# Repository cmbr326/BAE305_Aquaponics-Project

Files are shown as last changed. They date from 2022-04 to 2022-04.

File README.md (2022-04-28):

# BAE305_Aquaponics.Project

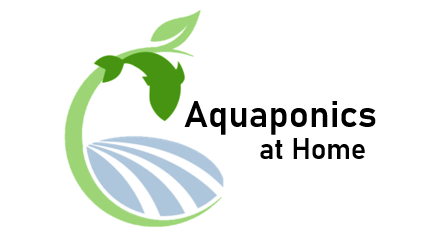
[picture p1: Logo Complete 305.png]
 

## Summary:

   The purpose of this project is to have an autonomous aquaponics system which includes an autonomous fish tank and plant growing environment. The two systems, the fish tank and the garden, work together by providing and filtering water for each other. The water from the fish tank is pumped into the garden when the soil moisture drops below a certain level, and the excess water from the garden precipitates back into the fish tank. Each of these components is vital to keep a livable environment for the fish while also benefiting the plants. The system comes equipped with a grow lamp to give the plants the light that they need on a scheduled basis. Each sensor in the aquaponics system includes displays for the user to properly monitor the vital aspects of the plants and fish's environment.
  
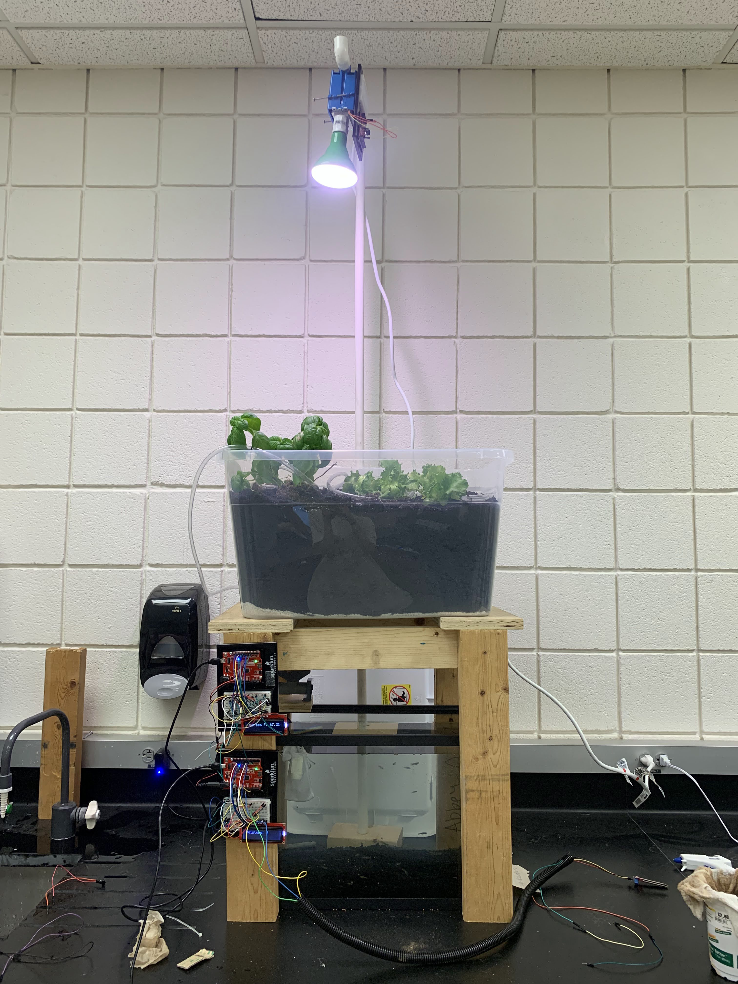
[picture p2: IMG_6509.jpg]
  
 
## Design Description: 

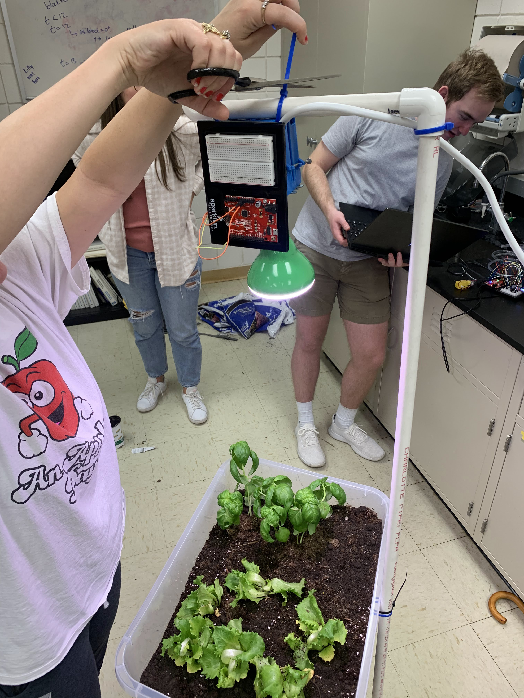
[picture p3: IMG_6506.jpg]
  
  
#### Supplies
- Arduino Uno (3)
- Water Pump (3V-5V Submersible Motor Pump)
- Motor (ElectroPeak DC Gear Motor)
- Temperature sensor (DS18B20 Temperature Sensor) 
- Soil Moisture sensor (SparkFun Soil Moisure Sensor with screw terminals SEN-13637)
- Light bulb
- Mobile outlet
- Fish tank
- Gravel 
- Fish
- Fish food 
- Large tote 
- Mesh screen
- Wood for suspension system
- Tubing 

#### Wiring Diagrams
Fish Tank Circuits


 
Soil Moisture Diagram

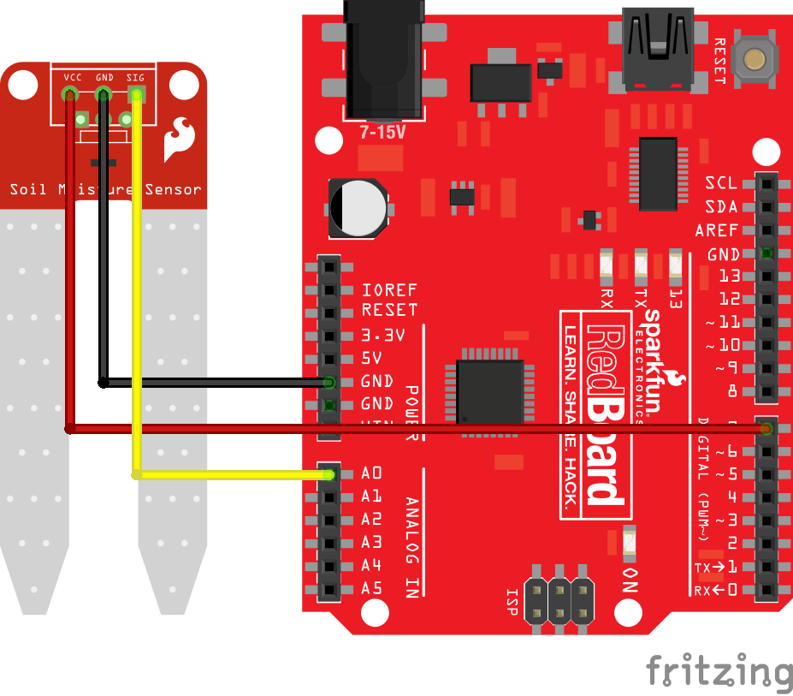
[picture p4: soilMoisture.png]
   
 
Soil Moisture Sensor and Pump 

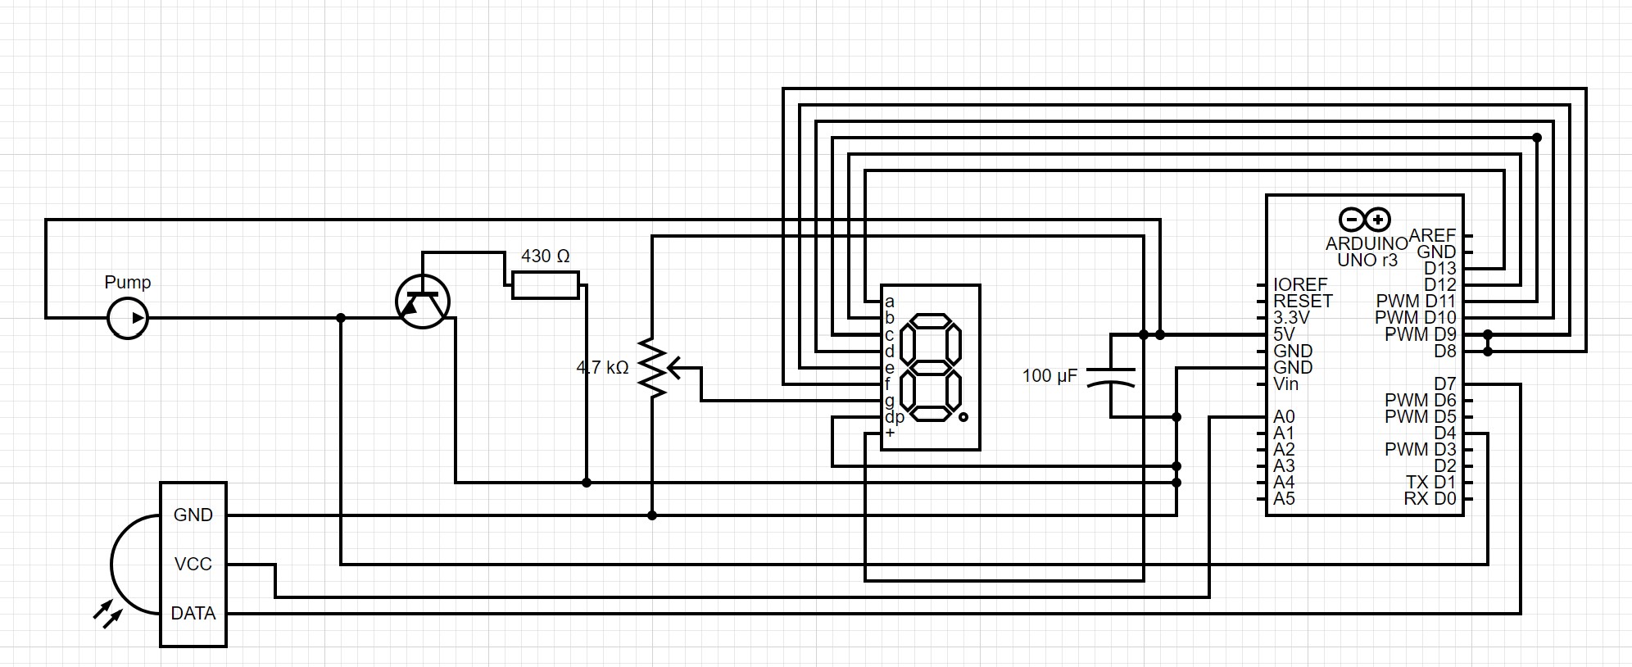
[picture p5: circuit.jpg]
   
 
 Temperature and Humidity Sensor
 
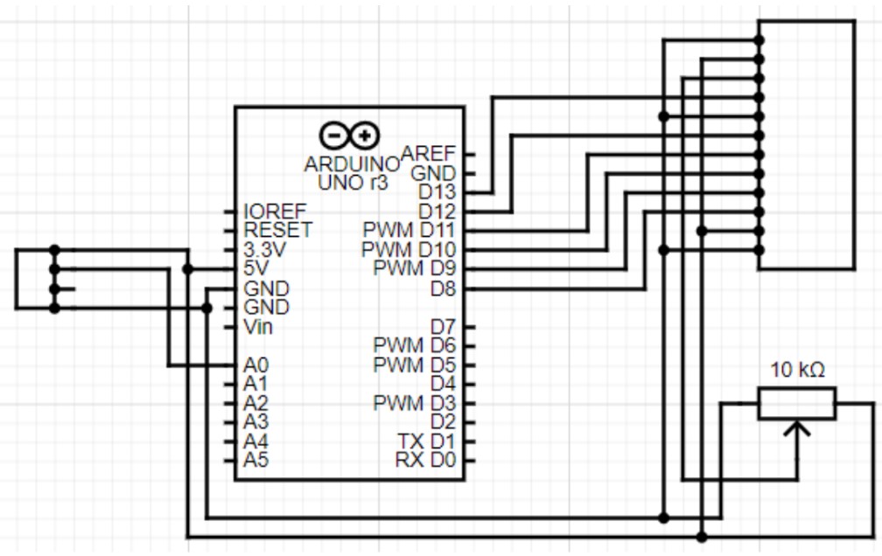
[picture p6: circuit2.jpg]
   
 
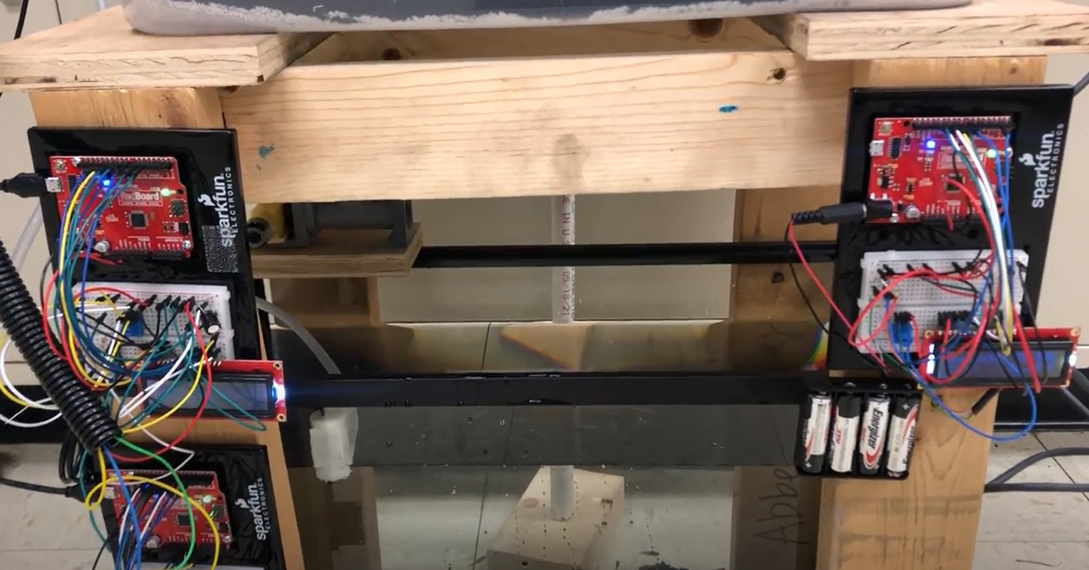
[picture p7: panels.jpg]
 

## Testing Description: 
Testing consisted of checking the sensor readings and the motor/pump functionality. Before soldering the wires and mounting the components to the build, it was important to check that all the components would operate correctly for their given job. All readings were checked to se if they were within reason.

   - The temperature sensor for the fish tank was tested to ensure that it was picking up the correct temperature and the code was able to display it correctly on the LCD screen.
     - The temperature was initially tested by using heat from a person's hand to see if the temperature displayed was in the correct range and was able to fluctuate appropriately. The temperature sensor was held in a hand for two minutes and the results of the temperature change were displayed on the connected LCD screen. 

   - The water pump was tested to ensure that it could function correctly submerged and that it was able to pump enough water up to the plants. 
     - The water pump was initially tested by writing a simple code to turn on the pump for five seconds then turn off the pump for five seconds. 
     - The strength of the water pump was then tested by placing the pump into a bin on water and hooking up the  five-foot tube and seeing if the water was being pumped up through the entire length of the tube and exiting through the other end of the tubing. 

   - The motor controlling the fish feeder was tested to ensure it could turn the 3-D printed feeder smoothly and that it supplied the correct amount of food. The motor should be able to turn the auger piece inside of the 3D printed feeder. 
     - The motor functionality and code was tested by seeing if it would run for one second every twelve seconds. This is because the final code was to have the motor turn every twelve hours. 
     - The amount of rotation was tested to ensure that the correct amount of food was being dispensed into the tank at each feeding. This was done by changing the time the motor would run.  

   - The soil moisture sensor was tested to ensure it worked properly before it was waterproofed and soldered together. 
     - After wiring the sensor to a board as the SparkFun diagram recommended, the sensor was placed in dry soil and moist soil to see what the levels were. For dry soil it was close to 0 and moist soil at the level desired was around 800.
     - When the sensor was ready, it was placed in the soil and connected with the pump so that when the level dropped below 800, it would trigger the pump to start pumping water.
     - The sensor was also connected to an LCD screen so that the moisture level was displayed.

   - The lamp was converted from DC to AC to control when the light was on.
     -  For the lamp, we first tested a cycle of turning on for 5 seconds and off for 5 seconds, which was a success. We then changed the code so that it would be on and off for the proper amount of time for the plants.

   - The temperature and humidity sensor were tested to ensure it worked properly before it was attached.
     -  A DHT 20 was originally tested to measure temperature and humidity, through testing it would return ‘failure to read’ messages. The DHT 20 would be replaced by a DHT 22 which would return readings that would were found to be accurate in comparison to a standard thermometer’s readings.

## Design Decision Discussion:

#### Water Pump:

   The water pump operated to move water from the fish tank to the irrigation system of the plant environment. Several design criteria were chosen in the placement and function of the pump. The model of the pump is the 3V-5V Submersible Motor Pump. The pump has a covering around it to ensure that neither large particulate nor fish are pulled into the valve. The pump is attached to the upper portion of the tank by Velcro. This placement allows for both convenient maintenance and minimal strain on the pump to move the water up around 1 foot. The pump operates off of a signal from the soil moisture sensor. 
   
#### Temperature Sensor:

   The DS18B20 temperature sensor allows the user to know the temperature in Fahrenheit of the tank water. This is important for varying fish and their needs. The temperature is displayed on the screen and informs the user on the temperature in real time. For the conditions and fish in the testing tank it was decided that there was no need for a heater. However, with the sensor it would be easy to monitor a heater if implemented.
  
#### Fish Feeder: 
 
   The Fish feeder consists of 7 individual 3D prints created on an Original Prusa Mini with PLA filament. These pieces include the hopper (which can hold 20 oz of food) and lid, two supporting joints to support and attach the system, the auger and auger tube, and the connecting joint for the motor. This was joined with tacky glue. The motor selected to turn the auger is the ElectroPeak DC Gear Motor. The system was then mounted with hot glue to a platform which was tied to the back left corner of the suspension system. This allows the feeder to hang over the tank and turn a decided amount of time, dispensing food directly into the tank. 
   
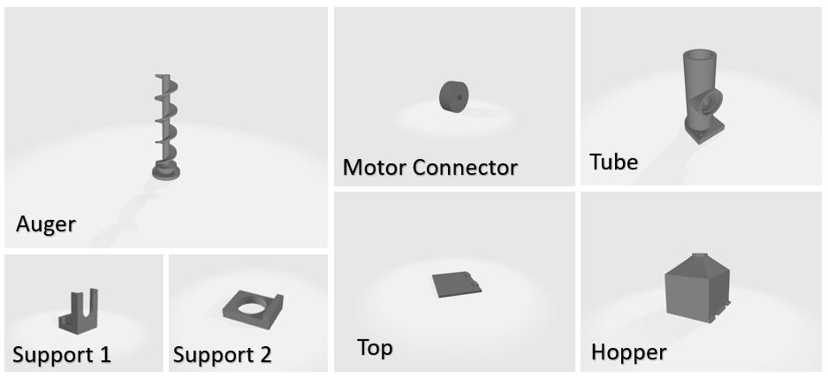
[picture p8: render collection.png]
   
   
#### Suspension System: 
   
   The suspension system was made of 2x4 wood to create two legs which could hold up the plant system above the tank. The need was for the center of the system to be open to allow water to drain from the holes of the planter back into the tank when necessary. This was done by creating two U shaped fixtures, then tying them together with another 2x4 on the sides on the platform. The suspension system also operates to hold up the electronics, including the fish feeder, Arduino, and screen display
   
#### Soil Moisture Sensor:
   
   The circuit for the sensor was mounted to the font of the table for the plant bed so it could reach the inside of the bed, while also being near the board for the pump so it could send the moisture readings to the pump. The sensor was waterproofed with hot glue to ensure water wouldn't ruin it. Based on the recommended soil moisture for the plants, lettuce and basil, the moisture level 800 was determined to be the minimum level. If the level drops below, the pump is signaled. The power supply is a pack of batteries that is also attached to the stand. The sensor was connected to an LCD screen so that the moisture level could be monitored. It will not show values under 800 because the pump is triggered and draws too much power, causing the screen to go blank. However, this isn't a problem since the value is not needed below 800. The following code was used for the soil moisture sensor and to signal the pump, some of the code was given by the SparkFun sensor.
   
   /*  Soil Moisture Basic Example
    This sketch was written by SparkFun Electronics
    Joel Bartlett 
    August 31, 2015

    Basic skecth to print out soil moisture values to the Serial Monitor 

    Released under the MIT License(http://opensource.org/licenses/MIT)
    */
    int pump = 4;
    int val = 0; //value for storing moisture value 
    int soilPin = A0;//Declare a variable for the soil moisture sensor 
    int soilPower = 7;//Variable for Soil moisture Power

    #include <LiquidCrystal.h>
    LiquidCrystal lcd(13, 12, 11, 10, 9, 8);

    //Rather than powering the sensor through the 3.3V or 5V pins, 
    //we'll use a digital pin to power the sensor. This will 
    //prevent corrosion of the sensor as it sits in the soil. 

    void setup() 
    {
    Serial.begin(9600); // open serial over USB
      pinMode(pump, OUTPUT);
      pinMode(soilPower, OUTPUT);//Set D7 as an OUTPUT
      digitalWrite(soilPower, LOW);//Set to LOW so no power is flowing through the sensor

      lcd.begin(16, 2);
      lcd.clear();

    }

    void loop() 
    {
    Serial.print("Soil Moisture = ");    
    //get soil moisture value from the function below and print it
    Serial.println(readSoil());

    //This 1 second timefrme is used so you can test the sensor and see it change in real-time.
    //For in-plant applications, you will want to take readings much less frequently.
    delay(1000);//take a reading every second

    lcd.clear(); 
    lcd.print("Moisture: ");                             
    lcd.setCursor(10, 0);                      
                
    lcd.print(val);  

    if (val <= 800){
      digitalWrite(pump, HIGH);
      delay(30000);
      digitalWrite(pump, LOW);

    }

    }
    //This is a function used to get the soil moisture content
    int readSoil()
  
    {

    digitalWrite(soilPower, HIGH);//turn D7 "On"
    delay(10);//wait 10 milliseconds 
    val = analogRead(soilPin);//Read the SIG value form sensor 
    digitalWrite(soilPower, LOW);//turn D7 "Off"
    return val;//send current moisture value
    }

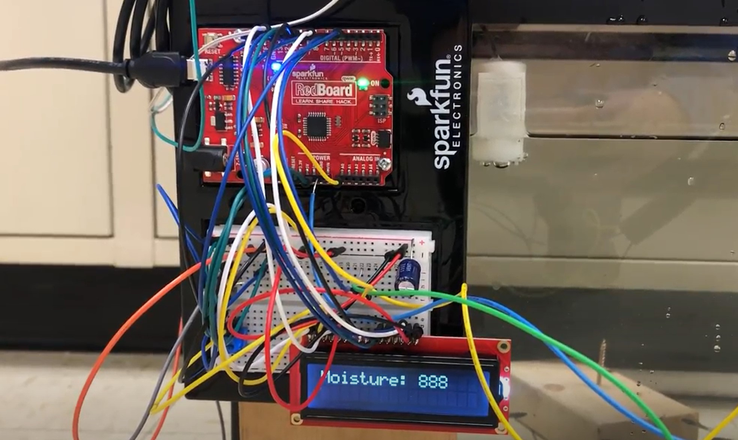
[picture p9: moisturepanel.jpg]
   
   
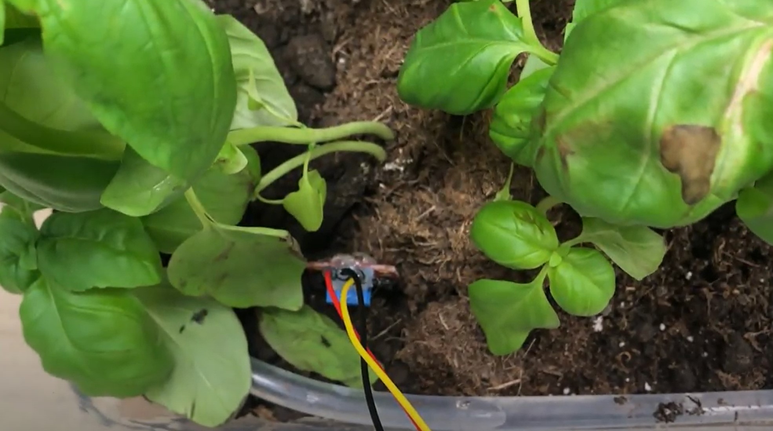
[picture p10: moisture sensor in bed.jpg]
   
   
#### Plant Bed:
   A clear plastic tote was used to hold the garden. Holes of about a ¼ in diameter were drilled about 2 in apart in the center region of the bottom of the tote.  Layers of fabric and a metal screen were placed at the bottom to keep dirt from falling through the holes. The rest of the tote was filled with dirt and plants on top. A tube was connected to the water pump and holes were put about 2 inches apart along the tube. The tube was snaked around the top of the garden so that water would be evenly dispersed.
   
#### Plant Lamp:
   The automatic grow light was made using an extension cord, AC outlet, relay, Arduino, and wires. The circuitry can be built by following  [This Tutorial](https://www.circuitbasics.com/build-an-arduino-controlled-power-outlet/). The grow light was hung off a PVC pipe connected to the stand so that it would be well-positioned to give all plants adequate light. The following code was used to time when the light was on and off.
   
       void setup() {
   
      // put your setup code here, to run once:
    pinMode(2, OUTPUT);

    }

    void loop() {
  
      // put your main code here, to run repeatedly:
  
    digitalWrite(2, HIGH);

    delay(36000000);

    digitalWrite(2, LOW);

    delay(50400000);
    }
   
#### Temperature and Humidity Sensor:
 
 A humidity and temperature sensor was researched and chosen. The circuitry of the LCD and sensor can be seen in the circuit section above. The Arduino was anchored to the base of the stand for display of results and the sensor is fashioned by zip ties on the inside wall of the tote to measure the humidity and temperature of the plants environment.
   
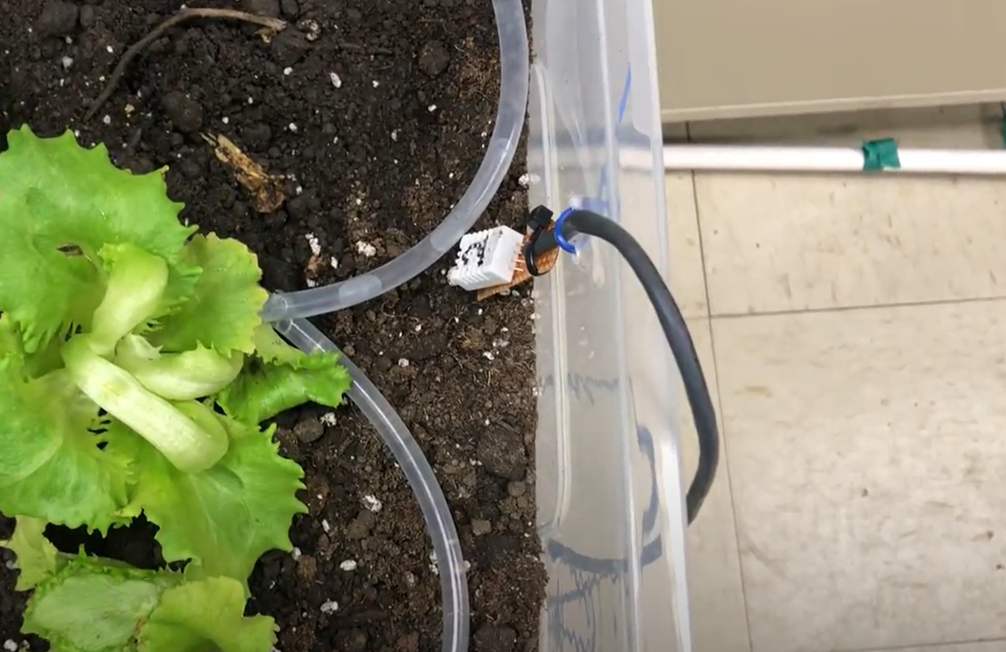
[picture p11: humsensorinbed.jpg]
   
   
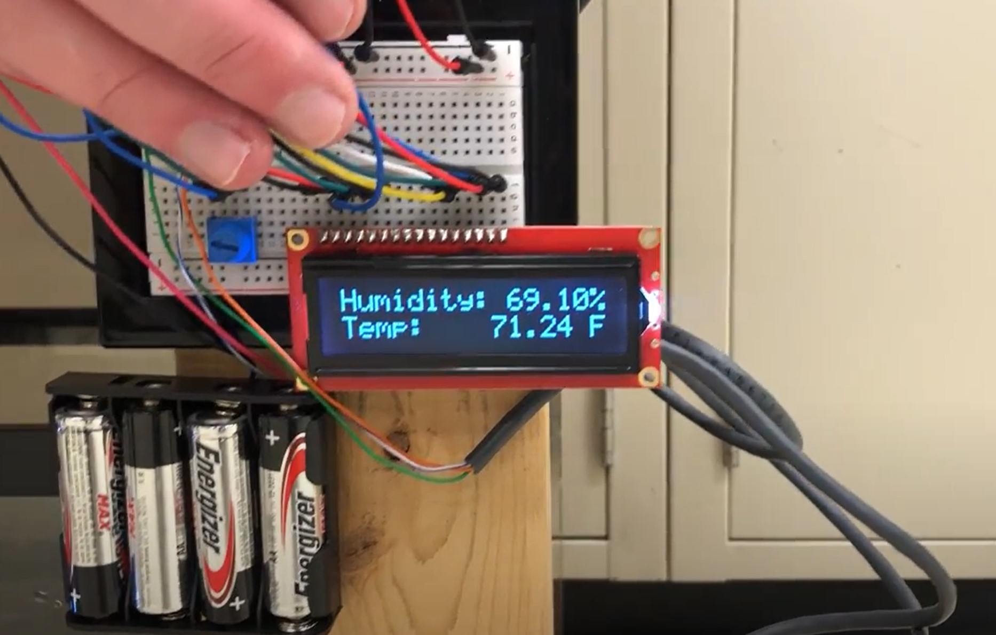
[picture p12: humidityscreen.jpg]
   
   
## Testing results:
   
#### Water Pump:

   The pump was able to turn on for five seconds and turn off for five seconds. The pump was also successful in pumping water through the entire five feet of tubing needed. This was enough "data" to ensure it would work properly for this use. 
   ### Temperature Sensor:
   The temperature read in the room was 70.2 Degrees Fahrenheit. The temperature reached after two minutes of holding the sensor in a hand was 98.5 Degrees Fahrenheit.
   
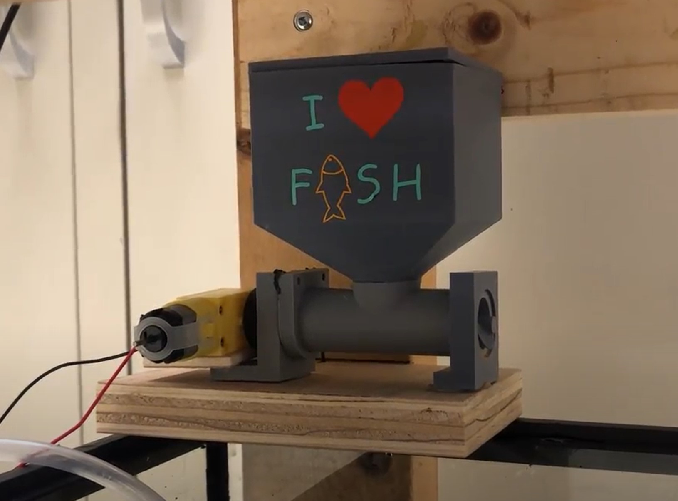
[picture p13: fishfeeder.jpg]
   
   
#### Fish Feeder:
   
   The fish feeder output 2 ounces of food when it was set to run for one second. The feeder output 1 ounce of food when run for half a second. The feeder output 0.5 ounces of food when it ran for a quarter of a second. The feeder holds approximately 30 ounces of standard goldfish pellets.
   
#### Soil Moisture Sensor:
   
   The moisture was around 880 when we first watered the plants before hooking up the pump system. This was the desirable moisture level. When the sensor was removed from the soil, the moisture level dropped which then successfully triggered the pump.
   
#### Plant Lamp:
   The lamp is able to turn on for 10 hours and off for 14 hours as long as it is plugged into the wall. These values were selected because it matches the night and day cycles for summer, which is the best time to grow small, green plants outdoors. The time cycles could be adjusted for different plant varieties
   
#### Temperature and Humidity Sensor:

   The DHT sensor constantly outputs temperature in Fahrenheit and humidity on the display. If powered by a laptop, temperature in Celsius as well as the heat index in Celsius and Fahrenheit is available through the Arduino code.
The lamp is able to turn on for 10 hours and off for 14 hours as long as it is plugged into the wall. 

## Test result Discussion:
The testing completed to test the functionality of the components does not require exact data outputs. This is because the testing done on the temperature sensor and the water pump were done just to ensure that they could read values and turn on and off. 
####  Water Pump:

   The testing done was functionality testing so no exact data outputs are needed. The volumetric amount of water does not need to be measured because the water is based on soil moisture and not a calculation based on water quantity. Testing done to ensure that the pump was strong enough to meet the needs of the system showed that it well exceeded possible limitations. 
#### Temperature Sensor:
   The temperature sensor read appropriate values based on room temperature and human hand temperature. Testing resulted in the decision to not include a heater in the system. This may need to be altered for alternate implementation tactics. 
   
#### Fish Feeder:
   After implementation of the testing tank, the feeder was initially over feeding. Using guppies, the decision was to crush food pellets into smaller pieces and insert those into the hopper. This allowed more particulate to gather in the auger than previously tested, so there was a change required in the turning time per feeding. Moving forward with implementation to other fish and food types, the capabilities of the auger should be considered. If larger food is used, it is necessary to compare the amount leaving the auger per turn. For the mentioned food and feeding needs, it was ultimately decided the quarter of a second motor run was sufficient in providing enough food to the fish without overfeeding. When the feeder is fully stocked, it will run for approximately 40 cycles of feeding, which is equal to 20 days.
#### Soil Moisture Sensor:
   The moisture sensor was reading appropriate values, around 880. The minimum moisture level of 800 was enough for the plants, while not taking too much water from the fish tank. When the sensor was removed from the soil and exposed to the air, it detects a value lower than 800 and triggers the pump. The only issue we ran into, was when the sensor detected a value lower than 800, the LCD screen would turn off because the pump was drawing too much power. It's okay if the value doesn't show below 800 because it should correct itself when it gets that low. 
#### Plant Lamp:
   The largest number usable for the variety of Arduino we are using is 2^32, which is about 2 billion. Our time values came in at well under this at only a few million. The plant lamp was found to be well-suited for our application, as we could use standard wall plugs connected to the Arduino which regulated the time. 
#### Temperature and Humidity Sensor:
   The readings are accurate, but the sensor is slow to react to extreme changes in temperature. Due to the size of the LCD only two readings will fit on the screen. While the sensor measures humidity and both temperature and heat index in Fahrenheit and Celsius, only humidity and temperature (Fahrenheit) are displayed since they are most relevant to the system.

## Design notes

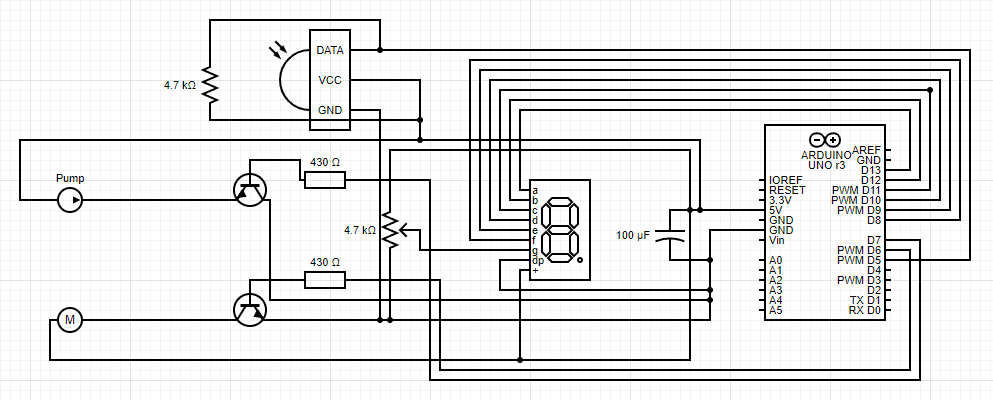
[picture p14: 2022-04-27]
AquaponicsCircuitF.png

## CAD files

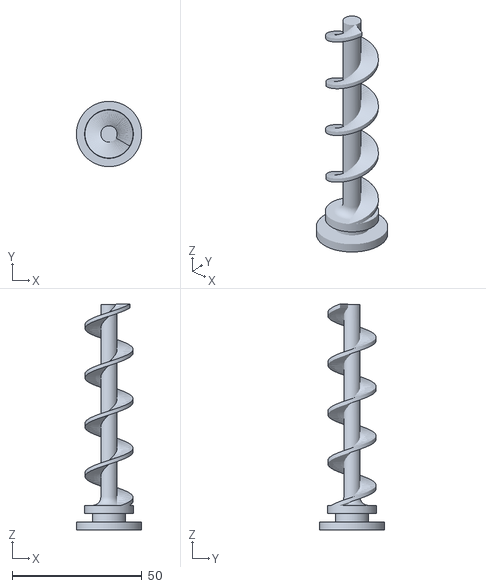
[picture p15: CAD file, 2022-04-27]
Auger (2).stl
25.2 x 25.2 x 87.2

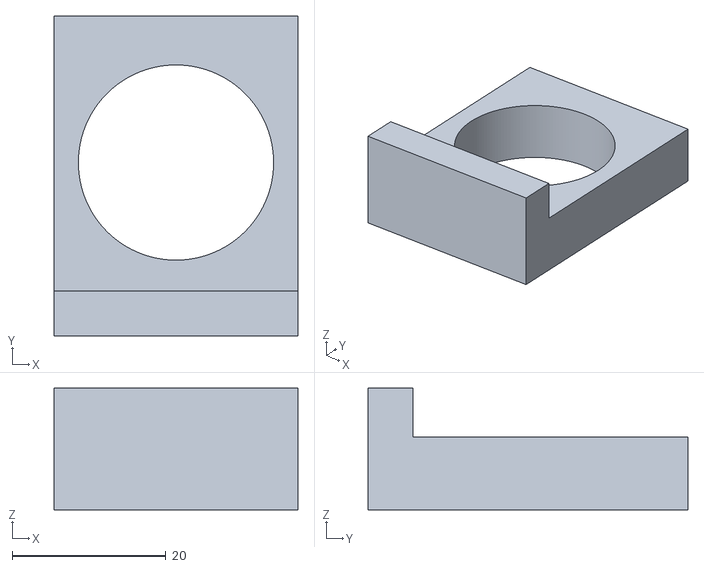
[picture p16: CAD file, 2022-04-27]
Tube_support (1).stl
31.8 x 41.6 x 15.8

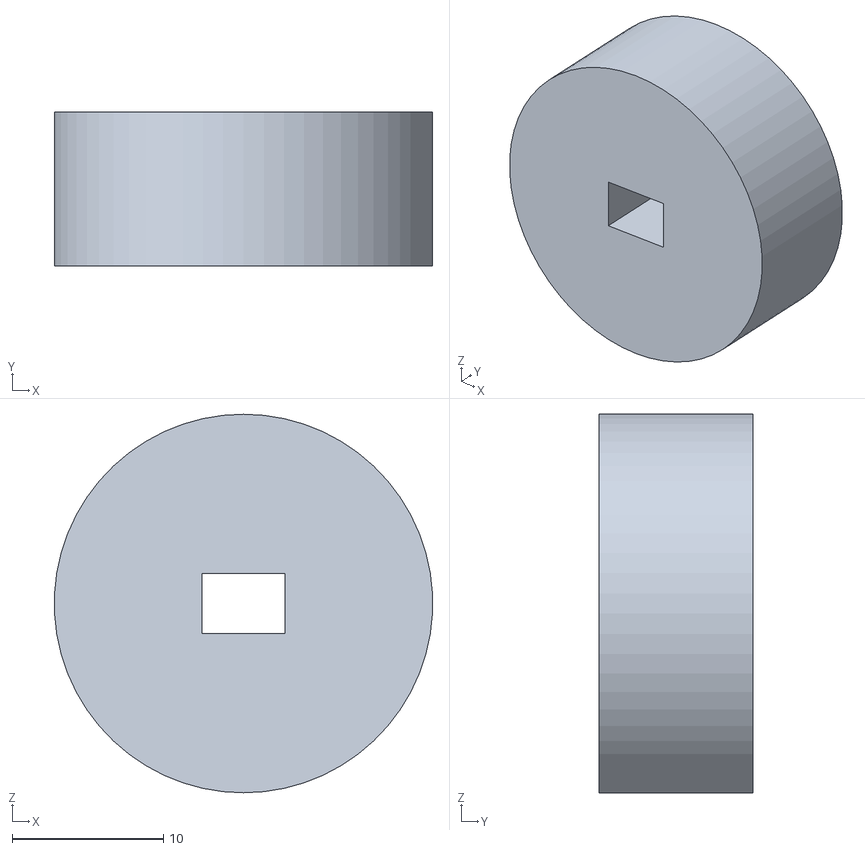
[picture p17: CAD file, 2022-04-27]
Motor Connector.stl
25.0 x 10.2 x 25.0

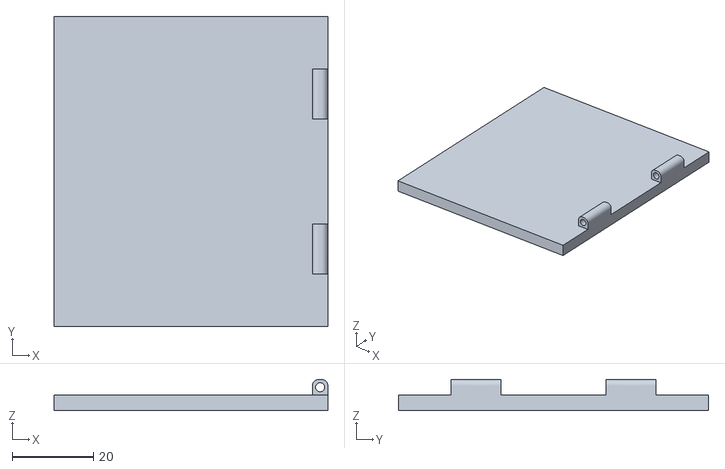
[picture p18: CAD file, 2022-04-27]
top (2).stl
67.3 x 76.2 x 7.62

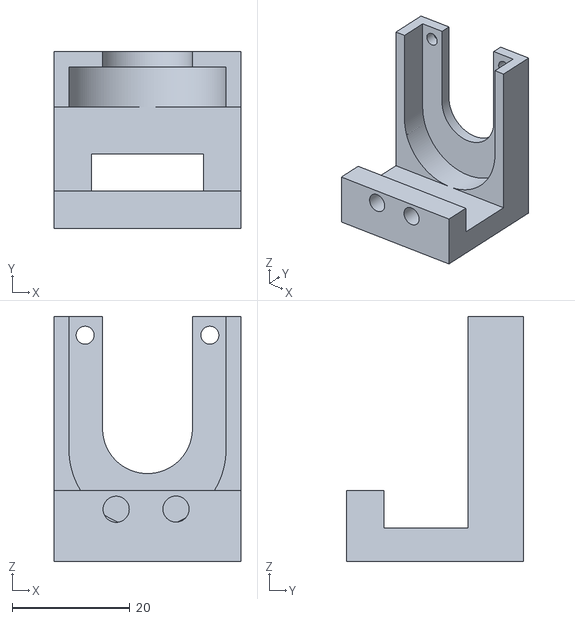
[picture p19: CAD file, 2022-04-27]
Motor_bracket (2).stl
31.8 x 30.1 x 41.6

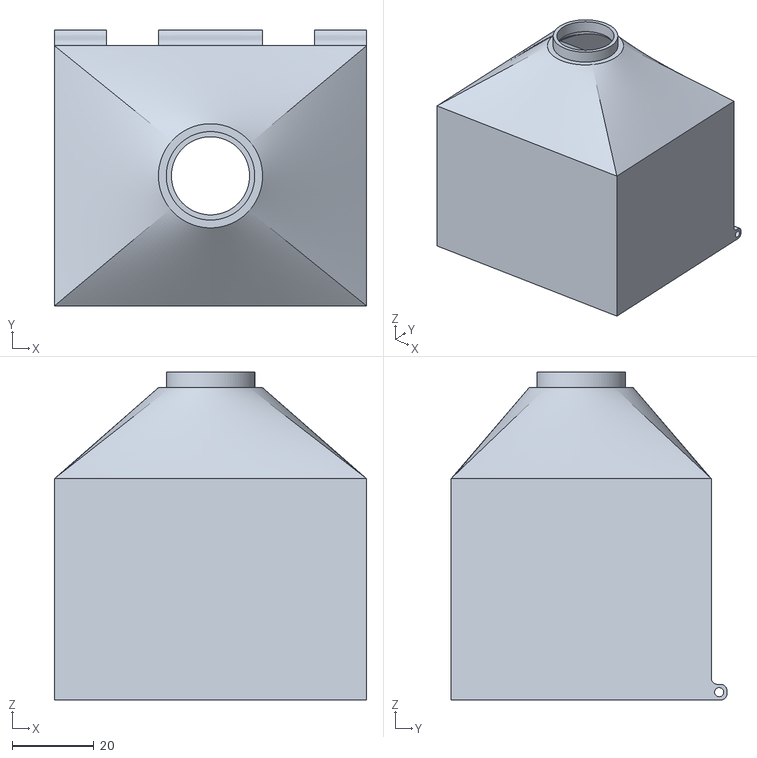
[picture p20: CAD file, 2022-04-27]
Hopper (2).stl
76.2 x 67.3 x 80.0

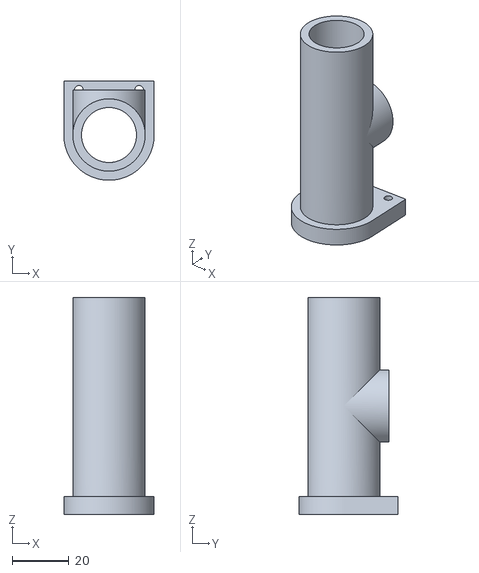
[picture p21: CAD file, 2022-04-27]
auger_tubev2 (1).stl
31.8 x 34.9 x 76.2

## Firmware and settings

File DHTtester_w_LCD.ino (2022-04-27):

// Example testing sketch for various DHT humidity/temperature sensors
// Written by ladyada, public domain

// REQUIRES the following Arduino libraries:
// - DHT Sensor Library: https://github.com/adafruit/DHT-sensor-library
// - Adafruit Unified Sensor Lib: https://github.com/adafruit/Adafruit_Sensor

#include "DHT.h"
#include <LiquidCrystal.h>          //the liquid crystal library contains commands for printing to the display

LiquidCrystal lcd(13, 12, 11, 10, 9, 8);   // tell the RedBoard what pins are connected to the display

#define DHTPIN 2     // Digital pin connected to the DHT sensor
// Feather HUZZAH ESP8266 note: use pins 3, 4, 5, 12, 13 or 14 --
// Pin 15 can work but DHT must be disconnected during program upload.

// Uncomment whatever type you're using!
//#define DHTTYPE DHT11   // DHT 11
#define DHTTYPE DHT22   // DHT 22  (AM2302), AM2321
//#define DHTTYPE DHT21   // DHT 21 (AM2301)

// Connect pin 1 (on the left) of the sensor to +5V
// NOTE: If using a board with 3.3V logic like an Arduino Due connect pin 1
// to 3.3V instead of 5V!
// Connect pin 2 of the sensor to whatever your DHTPIN is
// Connect pin 3 (on the right) of the sensor to GROUND (if your sensor has 3 pins)
// Connect pin 4 (on the right) of the sensor to GROUND and leave the pin 3 EMPTY (if your sensor has 4 pins)
// Connect a 10K resistor from pin 2 (data) to pin 1 (power) of the sensor

// Initialize DHT sensor.
// Note that older versions of this library took an optional third parameter to
// tweak the timings for faster processors.  This parameter is no longer needed
// as the current DHT reading algorithm adjusts itself to work on faster procs.
DHT dht(DHTPIN, DHTTYPE);

void setup() {
  Serial.begin(9600);
  Serial.println(F("DHTxx test!"));

  dht.begin();

  lcd.begin(16, 2);                 //tell the lcd library that we are using a display that is 16 characters wide and 2 characters high
  lcd.clear();                      //clear the display
}

void loop() {
  // Wait a few seconds between measurements.
  delay(2000);

  // Reading temperature or humidity takes about 250 milliseconds!
  // Sensor readings may also be up to 2 seconds 'old' (its a very slow sensor)
  float h = dht.readHumidity();
  // Read temperature as Celsius (the default)
  float t = dht.readTemperature();
  // Read temperature as Fahrenheit (isFahrenheit = true)
  float f = dht.readTemperature(true);

  // Check if any reads failed and exit early (to try again).
  if (isnan(h) || isnan(t) || isnan(f)) {
    Serial.println(F("Failed to read from DHT sensor!"));
    return;
  }

  // Compute heat index in Fahrenheit (the default)
  float hif = dht.computeHeatIndex(f, h);
  // Compute heat index in Celsius (isFahreheit = false)
  float hic = dht.computeHeatIndex(t, h, false);

  Serial.print(F("Humidity: "));
  Serial.print(h);
  Serial.print(F("%  Temperature: "));
  Serial.print(t);
  Serial.print(F("°C "));
  Serial.print(f);
  Serial.print(F("°F  Heat index: "));
  Serial.print(hic);
  Serial.print(F("°C "));
  Serial.print(hif);
  Serial.println(F("°F"));

  lcd.setCursor(0, 0);              //set the cursor to the 0,0 position (top left corner)
  lcd.print("Humidity:  ");
  lcd.print(h);
  lcd.print("%")

  lcd.setCursor(0, 1);              //move the cursor to the first space of the bottom row
  lcd.print("Temp:  ");
  lcd.print(f);
  lcd.print(" F");
}

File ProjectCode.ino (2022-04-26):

int pump=7; //initialize pump, feeder, time, and block variables
int feeder=6;
int t=0;    
int block=0;

#include <OneWire.h>  //initialize temperature sensor
#include <DallasTemperature.h>
#define ONE_WIRE_BUS 5
OneWire oneWire(ONE_WIRE_BUS);
DallasTemperature sensors(&oneWire);
 float Celcius=0;
 float Fahrenheit=0;
 
#include <LiquidCrystal.h> //initialize LCD
LiquidCrystal lcd(13, 12, 11, 10, 9, 8);

void setup() {   
pinMode(pump, OUTPUT);  //set motor pins as outputs
pinMode(feeder, OUTPUT);
 
lcd.begin(16, 2); //setup LCD
lcd.clear();      
lcd.setCursor(0, 0);                      
lcd.print("Degrees F: ");                

Serial.begin(9600); //start serial monitor
sensors.begin();
}
void loop() {  
lcd.setCursor(11,0);    //print temperature to LCD                        
lcd.print(Fahrenheit);      

t=millis()/3600000; //start timer function for feeder
Serial.println(t);
Serial.println(block);
if (t%12==0){
  if (block==0) {
    Serial.println("Feeder is running");
    digitalWrite(feeder,HIGH);
    delay(250);
    digitalWrite(feeder,LOW); 
    block=1;
  }
}
if (t%12==1){
  block=0;
}

sensors.requestTemperatures();  //read temperature and print to serial monitor
Celcius=sensors.getTempCByIndex(0);
Fahrenheit=sensors.toFahrenheit(Celcius);
Serial.print(" C  ");
Serial.print(Celcius);
Serial.print(" F  ");
Serial.println(Fahrenheit);
delay(1000);
}
